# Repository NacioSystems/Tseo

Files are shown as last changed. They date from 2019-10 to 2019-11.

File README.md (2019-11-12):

# Tseo
## de NacioSystems:

Versión 2.0
Fecha: 21/10/2019

Este proyecto es un robot llamado Tseo, que resuelve laberintos. Realizado por NacioSystems (O Milladoiro):

- - - 

### Introducción:

El robot está basado en la plataforma **Pololu Zumo Arduino**, al que se le incorporan tres sensores de distancia _VL6180_, uno en el frontal, y otros dos a cada lado. Se incorpora también un encoder acoplado a la cadena de desplazamiento. Los sensores _VL6180_ están centrados en la caja soporte de baterías. Por último, aunque no necesario, se incorpora el sensor _QTR_ frontal de Pololu Zumo, que se utiliza para leer la banda de entrada en meta.

El programa lee las paredes del laberinto a través de los sensores VL, con lo que puede determinar en que dirección se puede mover (no hay pared), hacia adelante, derecha, izquierda o dar la vuelta si es necesario. Cuando avanza cuenta los pasos del encoder con lo que puede saber cuanto se mueve y determinar si ha avanzado una casilla. Por otra parte, para hacer los giros utiliza el giróscopo _L3G_ incluido en el Zumo, garantizando que los giros son completos y se encuentra en la orientación de destino. Como se indicó anteriormente, a través del sensor _QTR_ frontal el robot puede saber cuando entra en la meta.

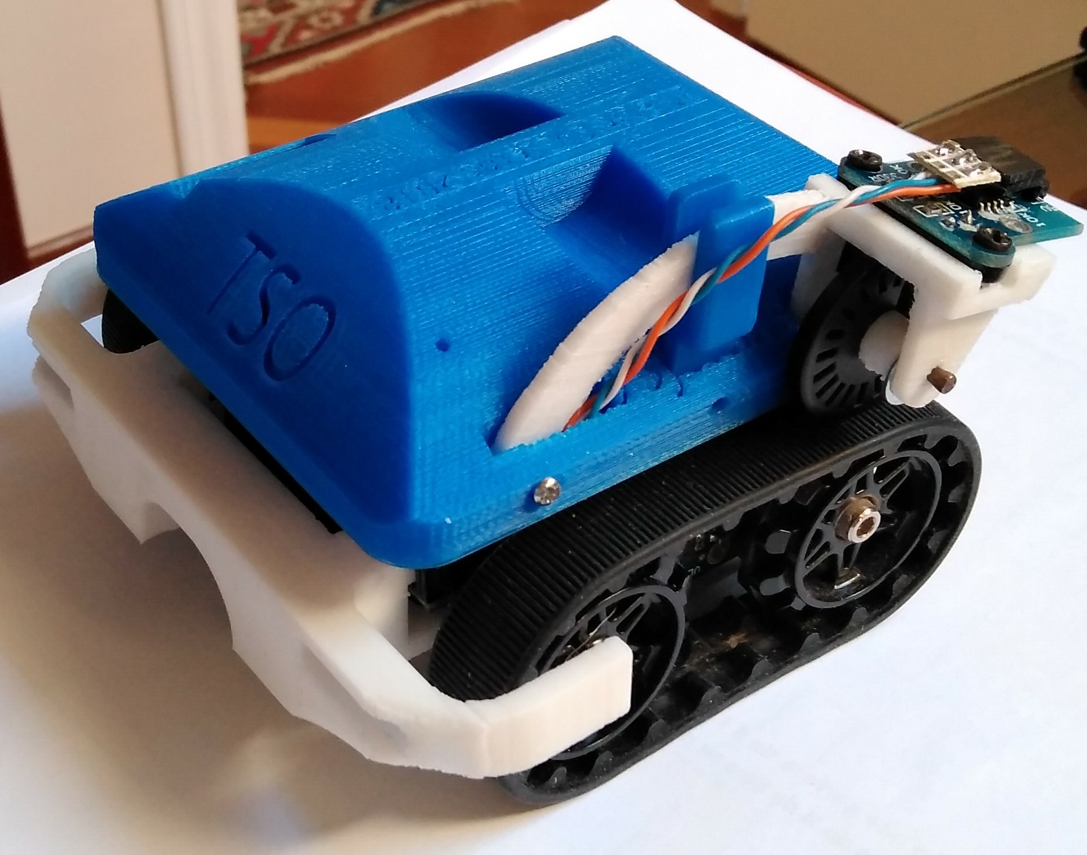
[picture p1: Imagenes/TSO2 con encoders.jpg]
Tseo Tseo listo


### Materiales:
* Pololu Zumo for Arduino (sin balda)
* Arduino UNO
* 3 x VL6180
* Zumo Reflectance Sensor Array (QTR)
* Encoder HC-020K, con rueda ranurada
* Piezas impresas 3D PLA
* Tornillos de 2mm de diámetro para sujeción Arduino y eje rueda ranurada
* Cables para conexionado, (recomendado CI perforado universal para soldar cables)

### Tablero:

El laberinto está formado por un tablero cuadrado de 256 celdas cuadradas (16x16), cada una de ellas de 18cm de lado.
El tablero está organizado en dos ejes (X, Y), de tal manera que el eje X está orientado en el sentido 0º / 180º, y el eje Y está orientado en el sentido perpendicular 90º / 270º. Para entender esta orientación pensemos en la pantalla del ordenador, 0º sería hacia arriba, 180º hacia abajo, 90º hacia la derecha y 270º hacia la izquierda. Cada vez que el robot avanza, se desplaza en el eje X o en el eje Y, de tal manera que si avanza hacia 180º, el eje X se incrementa, mientras que si avanza hacia 0º el eje X de decremeta. Por otra parte si avanza hacia la dirección 90º el eje Y se incrementa, y si avanza hacia 270º el eje Y se decrementa.

**Ejemplo de tablero y colocación de casillas (16,16), y orientación física:**

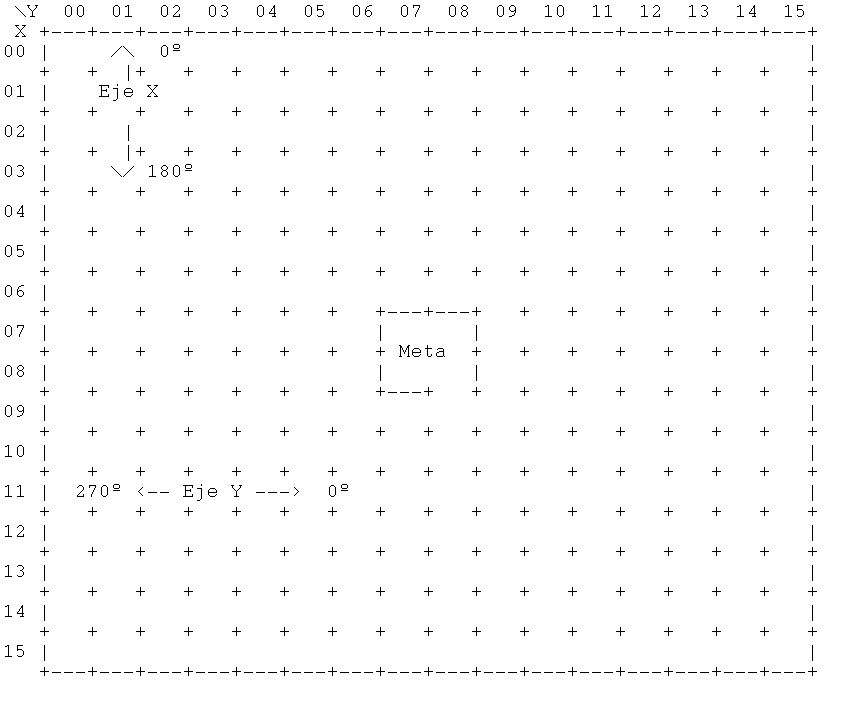
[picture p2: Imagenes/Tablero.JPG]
Tablero Tablero laberinto


### Giros:

Cada vez que el robot gira a la derecha su orientación inicial se incrementa en 90º, mientras que si gira a la izquierda su orientación inicial se decrementa 90º. No hay que decir que cuando da media vuelta supone un giro de 180º, o lo que es lo mismo dos giros de 90º. 

### Condiciones iniciales:

Se supone que la posición de inicio siempre es la misma, la casilla (0,0).
También se supone que la meta está siempre en el mismo sito, filas 7 y 8, columnas 7 y 8. La meta está cerrada totalmente a excepción de la entrada, que será siempre por la falta de muro entre las casillas (8,8) y (9,8).
El robot tendrá que saber en que orientación arranca, en sentido creciente del eje X o sentido creciente del eje Y, direcciones 180º o 90º respectivamente. Tseo utiliza el encoder, antes de inicio de la prueba, para indicarle la orientación de inicio, 180º por defecto, o 90º si se cambia.

Por otra parte Tseo, que no conoce el laberinto que va a resolver, puede elegir el sistema para recorrerlo y resolverlo entre tres opciones; regla de la mano derecha, regla de la mano izquierda o por inundación (en fase de pruebas). Para ello se utiliza el botón del Zumo, dependiendo del tiempo de pulsación de dicho botón. Una pulsación corta inicia el movimiento en base a la regla de la mano derecha, una pulsación de más de 1 segundo hace que arranque con la regla de la mano izquierda, pero si se pulsa más de 3 segundos utiliza la técnica de la inundación.

### Desplazamientos y giros:

Para los desplazamientos y giros se utilizan las rutinas de Pololu ZumoMotors y L3G TurnSensor. El robot se desplaza a la máxima velocidad que le permiten sus motores (de Minisumo), con la excepción de que tenga que hacer un giro, entonces reduce la velocidad en un 30% para compensar la inercia, que es bastante. Debido a su masa, en el momento que detecta el cambio de condiciones, por ejemplo un cruce de caminos, el robot recorre una distancia considerable después del frenazo, lo que dificulta situarse en la posición correcta para los giros. Para ello utiliza una velocidad menor y cuenta los pasos desde que toma la decisión de frenar para saber si está bien situado. Lo mismo ocurre en los giros, controlados por giróscopo, una vez completado el giro la inercia del robot hace que gire un poco de más, sobre 2º, por lo que, en función de la velocidad de giro, hay que completar ángulos más cortos, de unos 88º.

### Programa:

El programa está realizado con el IDE Arduino, para su programación directa a través de cable USB. En la carpeta software se puede ver el programa comentado. El pineado está explicado en los comentarios, sólo es necesario montar el cableado para el encoder y los sensores VL, utilizando los pines de expansión que hay en la placa Zumo. En mi caso utilicé pines hembra en la parte exterior de la *shield* y en el puerto de expansión frontal.

Una vez configurados todos los sensores y sistemas de Tseo, el programa admite el cambio de configuración por defecto, ya sea la selección de la regla mano derecha, mano izquierda, o la conmutación de los ejes del laberinto. La selección de la regla de inicio es a través de una pulsación larga del botón de inicio. Por defecto sale en el eje *X*, pero si el laberinto es diferente se selecciona la salida en el eje *Y* mediante un giro de la rueda del encoder antes del inicio. Tseo responderá con unos pitidos de que ya está configurado.

Pulsando el botón de inicio, una pulsación corta, empieza a resolver el laberinto, de tal forma que cada vez que encuentra un cruce decide tomar una decisión que guarda en la memoria. Lo mismo en el caso de que llegue a una pared y no pueda seguir, para dar media vuelta. Cada vez que se da media vuelta sabe que ese camino que recorrió desde la última decisión es incorrecto, por lo que elimina de la memoria ese camino cambiando la penúltima decisión tomada, por otra más adecuada. De esa manera va recorriendo el laberinto y guardando las decisiones tomadas, cuando detecta que en su camino el sensor de líneas delantero reconoce el color blanco, sabe que llegó a la meta. Tambien sabe que está en la meta por la casilla en la que se encuentra, pues através del _encoder_ y los giros sabe en que posición está. Una vez en la meta se para y espera que lo coloquen en la casila de salida de nuevo para iniciar de nuevo el recorrido, esta vez por el camino más corto, teniendo en cuenta las decisiones que fue almacenando en la memoria.

Tseo podría volver sólo a la casilla de origen recorriendo el camino inverso que tiene guardado en la memoria, pero dependiendo de la complegidad del laberinto, y el tiempo de competición que resta, parece más rápido y adecuado llevarlo directamente en brazos al origen. Esta función se implementará en la siguiente versión, de tal manera que si no se recoge de la meta en un tiempo determinado, Tseo decida volver el solo.

Tseo no necesita guardar todos los giros y avances que hace en la memoria, lo que le permite ahorrar mucha RAM y dedicarla a otros asuntos. Esto es, en el caso de que esté recorriendo un pasillo sin ningún cruce, aunque tenga que hacer giros a derecha o izquierda, independientemente de las casillas que avance, seguirá el único camino posible pero no tomará nota de los giros, ya que no aportan información para resolver el labertinto.

Cuando la decisión a tomar es un giro, comprueba su orientación respecto de la marcación en grados del giróscopo y hace girar los motores uno en un sentido y el otro en el inverso, dependiendo si es un giro a derechas o a izquierdas. Va leyendo la marcación del giróscopo y hasta que no alcanza los 90º de giro, mantiene los motores en marcha.

Cuando avanza va comprobando a través de los sensores VL si tiene o no pared a la derecha, izquierda o delante, de esa manera sabe si llegó a un cruce o todavía está pasando el cruce al que había llegado.

Al final, después de recorrer todo el laberinto, hace un pequeño baile mientras toca una alegre canción.

Por otra parte, a través del encoder, que está conectado a las interrupciones (pin 2), va contando los pasos que avanza, de tal manera que recorrida la longitud de una casilla y sabiendo la orientación en la que está, actualiza su posición. De esa manera sabe en que casilla está en cada momento, y reconoce por su situación cuando está en la casilla de meta. Esta funcionalidad está pensada para utilizar el sistema de resolución por _inundación_, todavía en evaluación por las capacidades y potencia del **ATmega328P** del Arduino. Otros robots que trabajan por la regla de la _inundación_ disponen de procesadores más rápidos y potentes, hacerlo con un **ATmega328P** a 16 MHz es todo un reto.

### Construcción:

La construcción es muy sencilla, la base es la plataforma **_Pololu Zumo for Arduino_**, al que se le ha retirado la balda de Minisumo. La plataforma se complementa con un **_Arduino Uno_**, el sensor **QTR** del **_Zumo Refectance Sensor Array_**, los tres sensores de distancias **_VL6180_** y el encoder **_HC-020K_**.

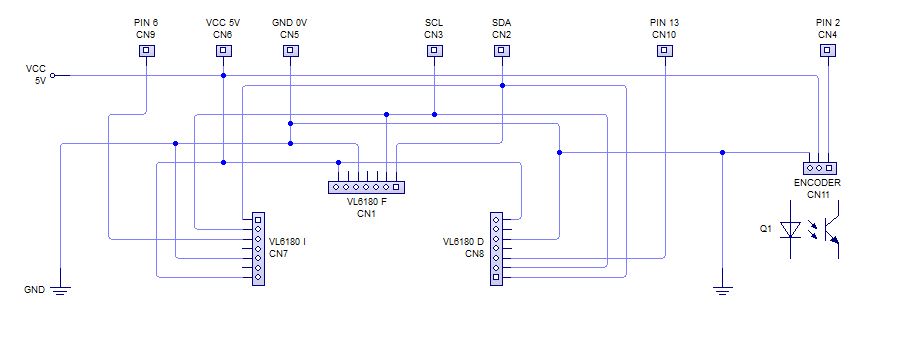
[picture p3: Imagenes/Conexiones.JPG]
Esquema de conexión


Lo único que hay que construir es el cableado de conexión de los **VL6180** y el encoder al Arduino, así como los soportes del encoder y los VL. *_La Pololu Zumo Shield for Arduino_* se encarga de realizar las conexiones con el resto de componentes, teniendo en cuenta que deberemos dejar los puentes de lectura de la tensión de la batería (A1) y del interfaz **_I2C_** (SCL, SDA), necesarios para comunicarse con el giróscopo **L3G** y los sensores **VL6180** a través de la librería _Whire_.  Para la conexión de la tarjeta _Bluetooth 5V_ es necesario montar tambien una tira de 4 pines hembra en el panel de expansión frontal izquierdo de la _shield_.  El el programa para Arduino están indicadas las conexiones de cada pin.

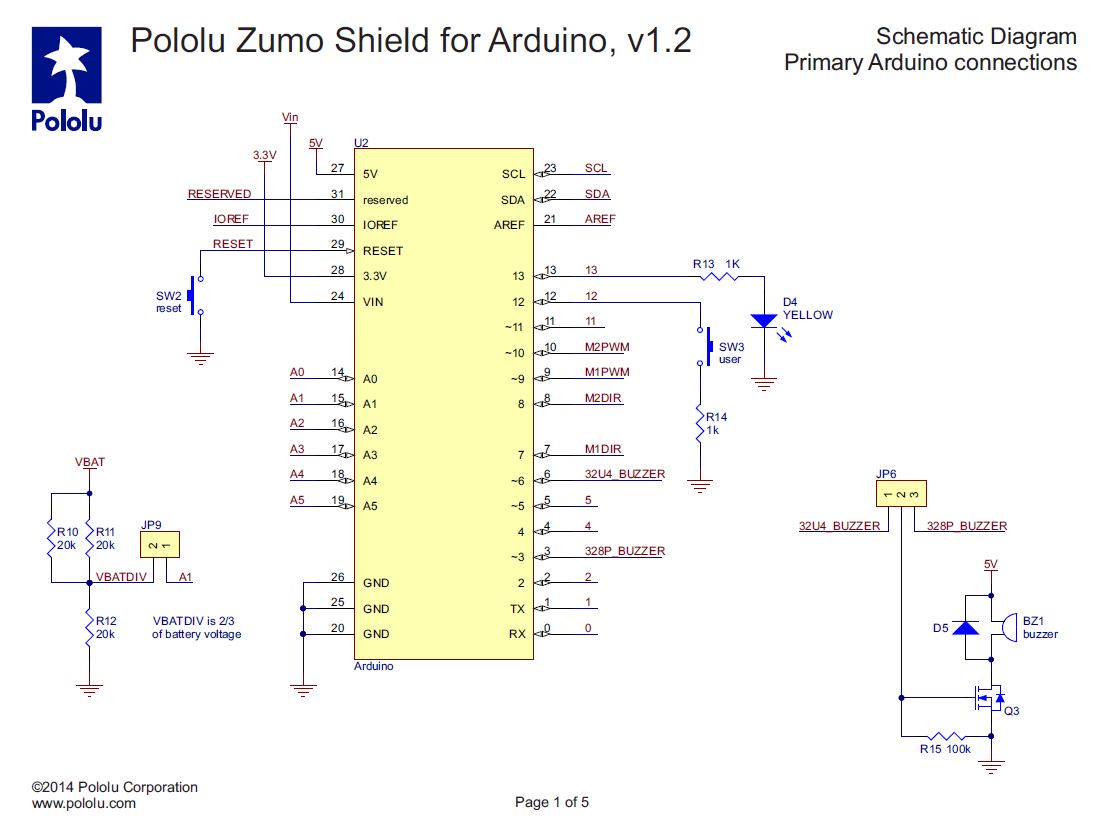
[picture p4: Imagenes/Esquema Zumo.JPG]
Esquema Zumo Arduino Esquema Pololu Zumo Arduino


Dependiendo de los motores que incorpore el Zumo, habrá que realizar ajustes a las velocidades para adaptarlas a la inercia del robot. En la fase de desarrollo me resultó imprescindible incorporarle un parachoques a Tseo, ya que las dimensiones de las cadenas hacen que en caso de derrapar o desplazamiento, las cadenas rocen con las paredes levantando al robot, creando un caos, incluso subiendo las paredes.

Tseo en construcción

La carcasa incluye un hueco muy práctico para instalar el interface _Bluetooth_ (HL05 - HL06), por si se quiere hacer un seguimiento del funcionamiento desde un terminar remoto.

También incluye un orificio para instalar un mástil, para llevar la bandera de Tseo, con la que se paseará de modo triunfante por el laberinto. El mástil puede ser un palillo de madera de los utilizados para las brochetas. La bandera está impresa en papel.

### Piezas impresas:

En la carpeta de piezas impresas, están los modelos Stl del soporte del encoder, del parachoques protector y la carcasa de Tseo, que le dan esa personalidad tan destacada.

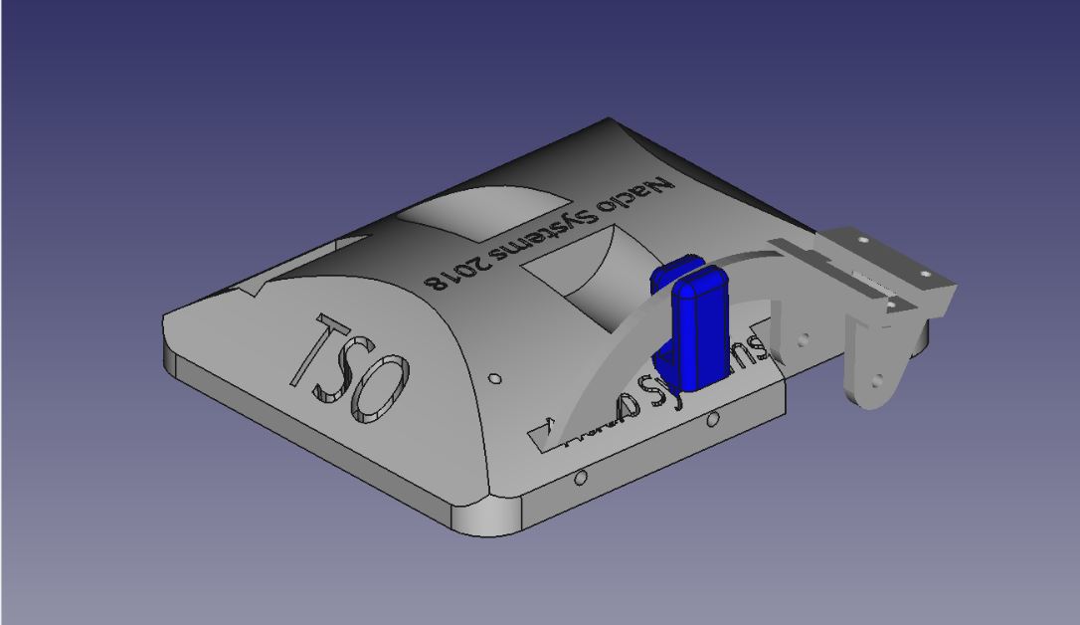
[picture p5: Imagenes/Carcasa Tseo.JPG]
Carcasa Tseo


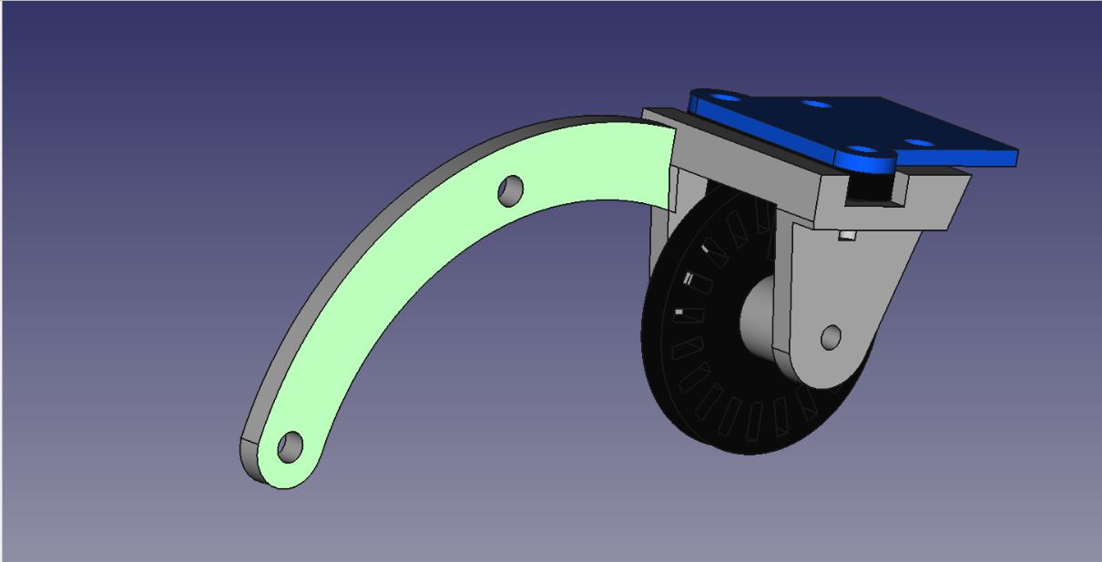
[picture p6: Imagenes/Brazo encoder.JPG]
Brazo encoder Brazo Encoder


### Referencias:

* *[Pololu Zumo for Arduino][1]*

* *[Aduino UNO R3][2]*

* *[Pololu Zumo Refectance Sensor Array][3]*

* *[Sensor LIDAR VL6180][4]*

* *[Encoder CNZ1120][5]*

* *[Encoder HC-020k][6]*

* *[Ejemplos Pololu][7]*

* *[Reglamento Laberinto OSHWDEM][8]*

### Autor:
**Ignacio Otero**

### Agradecimientos:

Muchas gracias **Bea** por tu colaboración en la revisión y corrección de esta página.

### Licencia:
Todos estos productos están liberados mediante Creative Commons Attribution-ShareAlike 4.0 International License.

[1]:https://www.pololu.com/product/2506

[2]:https://store.arduino.cc/arduino-uno-rev3

[3]:https://www.pololu.com/product/1419

[4]:https://www.adafruit.com/product/3316

[5]:https://tienda.bricogeek.com/componentes/39-fotointerruptor-cnz1120.html

[6]:https://www.amazon.es/Velocidad-HC-020K-Medici%C3%B3n-fotoel%C3%A9ctrico-Encoders/dp/B00MA63ZCW

[7]:https://github.com/pololu/zumo-shield

[8]:http://rules.oshwdem.org/labirinto_es

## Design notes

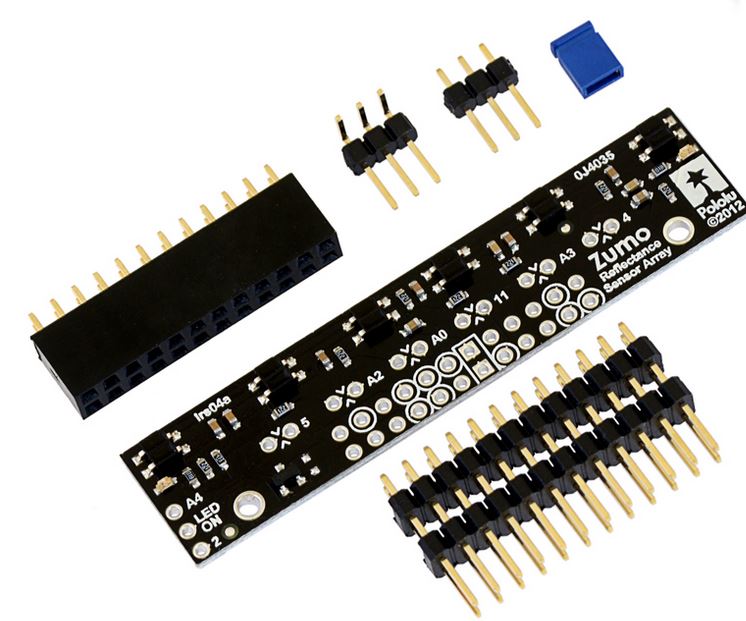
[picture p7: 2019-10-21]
Imagenes/QTR.JPG

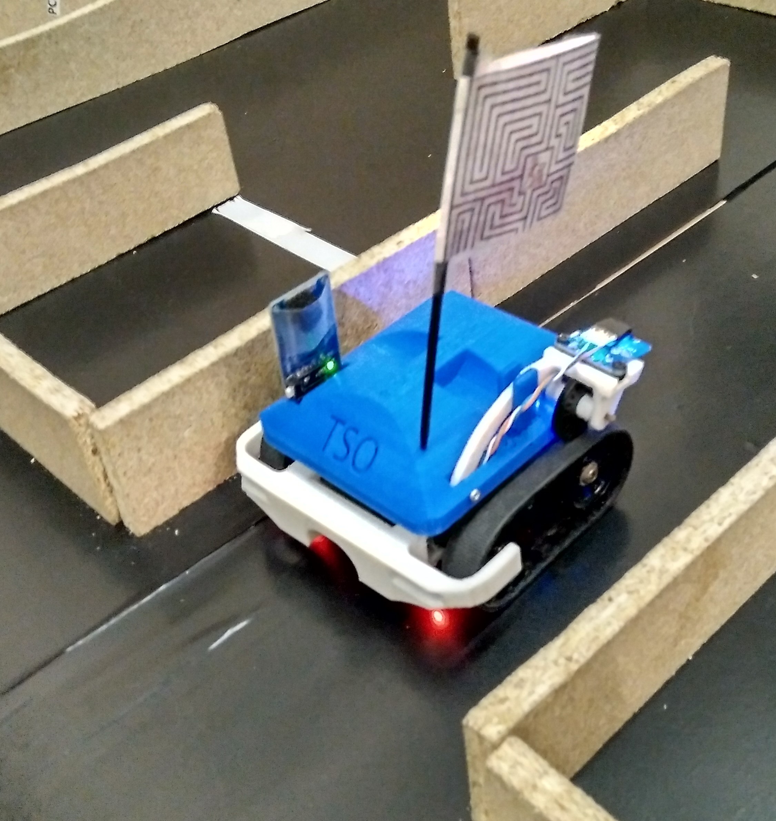
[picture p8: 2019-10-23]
Imagenes/Tseo en laberinto.jpg

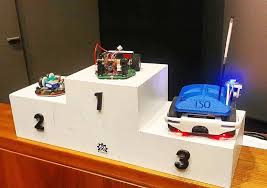
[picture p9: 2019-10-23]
Imagenes/Premios 2018.jpg

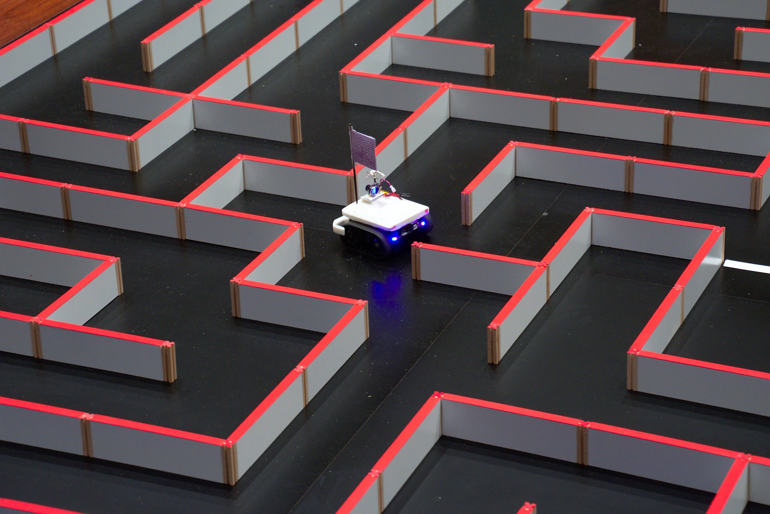
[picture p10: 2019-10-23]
Imagenes/Teseo 1 en Oshwden 2018.JPG

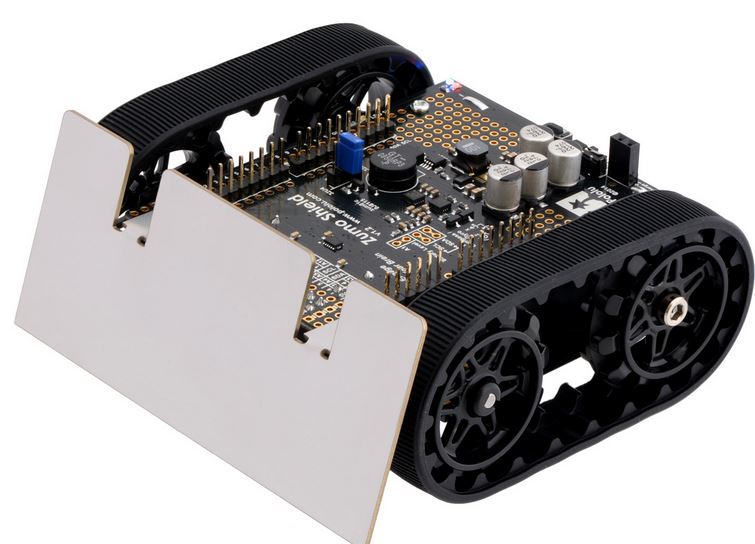
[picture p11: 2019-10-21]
Imagenes/Zumo2.JPG

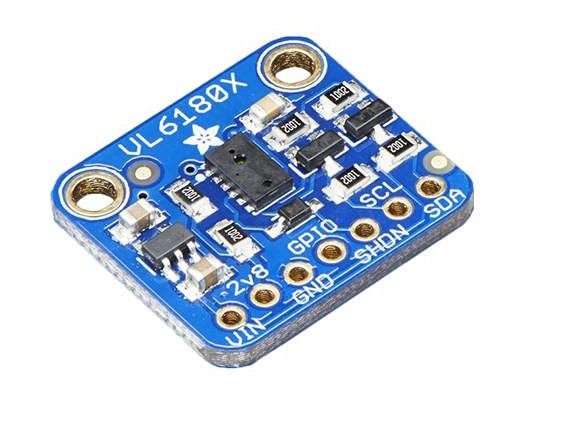
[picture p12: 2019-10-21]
Imagenes/VL6180.JPG

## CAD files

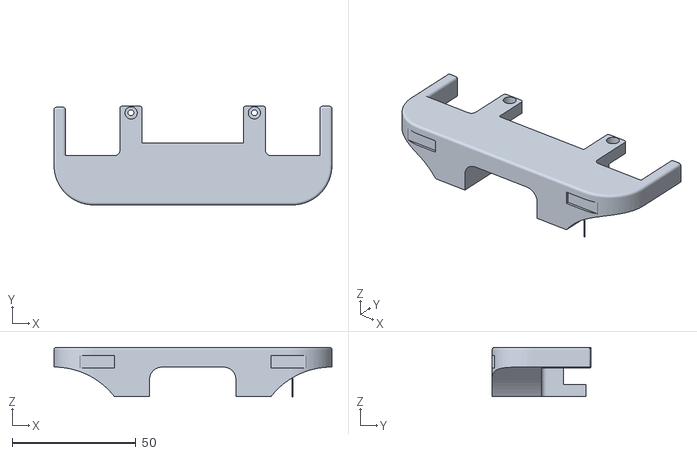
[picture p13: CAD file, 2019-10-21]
Partes Impresas/Parachoques.stl
112.6 x 40.0 x 20.0

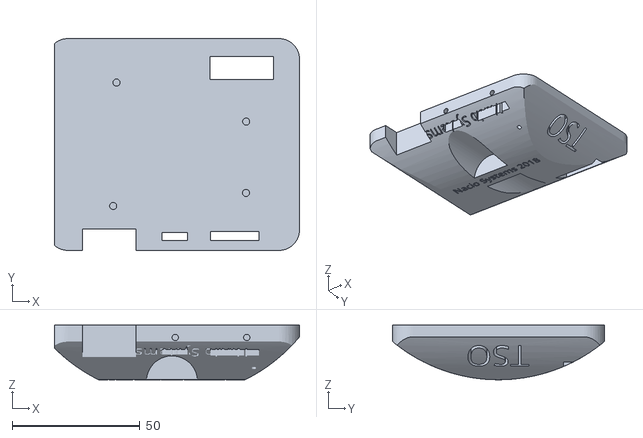
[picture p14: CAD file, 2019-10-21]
Partes Impresas/Cuerpo.stl
95.9 x 82.9 x 21.4

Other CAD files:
Partes Impresas/Brazo Encoder.stl

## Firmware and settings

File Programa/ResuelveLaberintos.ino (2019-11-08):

// RESUELVE LABERINTOS
// VERSIÓN 8.0 29/10/2018
// Por Ignacio Otero
// Ayuda de la idea de Pololu

// PINES USADOS EN ESTA VERSIÓN (19)
// BlueTooth y Serial (2) = 0, 1
// Motores Zumo (4) = 7, 8, 9, 10
// Sensor IR Zumo (7) = A0, A2, A3, 2, 4, 5, 11
// Buzzer Zumo (1) = 3 
// LED sólo en el setup, es compartido con Shutdown VLD (1) = 13 
// Pulsador Pushbutton Zumo (1)= 12
// Shutdown de sensores LIDAR VL medidores de distancia (1) = 6, 13
// Batería Zumo (1) = A1 afectado por jumper de batería
// I2C (2) = A4, A5
// Lector de interrupciones 0 por pin 2 para contar los pasos
// Si es necesario se puede utilizar A1 desconectando el jumper de la batería
// En caso de necesidad podría utilizarse los pines 7 y 8 (MDir1/2)
// como salidas digitales, siempre con motores parados o QTRSensor desactivado.

// CONFIGURACIÓN

// Para manejar el giróscopo L3G necesitamos I2G, librerias Wire
#include <Wire.h>
#include <L3G.h> // Consume 13 bytes
#include <TurnSensor.h> /* Esta librería requiere que se denomine
                        la clase L3G como "gyro", ya que es el nombre
                        que utiliza. Consume 69 bytes.
                        Se elimina de la librería TurnSensor el encendido del Led
                        Nombres de variables o constantes utilizados que no aparecen 
                        en el programa pero vienen definidos en las librerías:

                        ZUMMO_BUTTON es el nombre del botón del Zumo, pin 12

                        turnAngle    es una varible de la librería TurnSensor que
                                     indica el ángulo de giro relativo
                                     desde la medición anterior
          
                        turnAngle1   es una constante que representa el valor
                                     del giro de aproximadamente un ángulo de 1 grado
                                     Pololu recomienda que para un ángulo de 45º, se
                                     representa por el valor 0x20000000. 
                                     Un grado serían 45 veces menos.
           
                        turnRate     es la velocidad de giro instantánea, respecto de la
                                     velocidad anterior, en unidades de 0,07 grados por s.
                                     Se representa entre -180º y 180º, en sentido contrario
                                     a las agujas del reloj
                                     */

#include <VL6180X.h>    // Es la libreria de Polulu para los sensores LIDAR VL

// Tambien incluimos las librerias de Zumo
#include <ZumoMotors.h> // Consume 2 byte de memoira OK
#include <ZumoBuzzer.h> // Consume 2 bytes de memoria OK
#include <Pushbutton.h> // Consume 8 bytes de memoria OK
#include <QTRSensors.h> // Va con ZumoReflectanteSensorArray
#include <ZumoReflectanceSensorArray.h> // Consume 60 bytes de memoria


#define Parada 0
#define turnSpeed 200     
#define straightSpeed 200 
#define adjustSpeed 150
#define LED 13
#define QTREmiterPin 2  

#define RANGE 1
#define VLIzquierda 0x29     //0010 1001 Address I2C Izquierda
#define VLDerecha 0x30       //0011 0000 Address I2C Derecha
#define VLFrontal 0x46       //0100 0110 Address I2C Frontal 
#define TIzquierda 6         // Shutdown del sensor Izquierda
#define TDerecha 13          // Shutdown del sensor Derecha

// Definimos el giróscopo
L3G gyro; // Esta denominación para el L3G es necesaria por
          // la librería TurnSensor.h.

// Definimos motores
ZumoMotors motors;

// Definimos un altavoz buzzer
ZumoBuzzer buzzer;

// Definimo el pulsador de arranque
Pushbutton button(ZUMO_BUTTON); //Turnsensor utiliza el nombre de button

#include <avr/pgmspace.h>  // Esto nos permite referirnos a datos en el espacion de programa (i.e la flash)
// almacenando esta fuga en el espacio de programa usando la macro PROGMEM.  
// Despues podremos tocar directamente desde el espacio de programa, sin necesidad de cargarlo
// todo en la RAM primero.
const char fugue[] PROGMEM = 
  "! O5 L16 agafaea dac+adaea fa<aa<bac#a dac#adaea f"
  "O6 dcd<b-d<ad<g d<f+d<gd<ad<b- d<dd<ed<f+d<g d<f+d<gd<ad"
  "L8 MS <b-d<b-d MLe-<ge-<g MSc<ac<a ML d<fd<f O5 MS b-gb-g"
  "ML >c#e>c#e MS afaf ML gc#gc# MS fdfd ML e<b-e<b-"
  "O6 L16ragafaea dac#adaea fa<aa<bac#a dac#adaea faeadaca"
  "<b-acadg<b-g egdgcg<b-g <ag<b-gcf<af dfcf<b-f<af"
  "<gf<af<b-e<ge c#e<b-e<ae<ge <fe<ge<ad<fd"
  "O5 e>ee>ef>df>d b->c#b->c#a>df>d e>ee>ef>df>d"
  "e>d>c#>db>d>c#b >c#agaegfe f O6 dc#dfdc#<b c#4";

// Definimos el sensor delantero QTR
// Definimos una clase de sernsor reflectante frontal, sin pin de emisión, no apaga los IR Leds
ZumoReflectanceSensorArray sensorIR(QTREmiterPin); 

// Definimos un array para almacenar los valores del sensor
#define NUM_SENSORES 6
unsigned int ValoresSensor[NUM_SENSORES];
#define NIVEL_DISPARO_QTR  300 // Es el valor de decisión, en microsegundos, tenía anteriormente 300 para borde blanco, 900 cartón marrón borde negro
                               // Hay que pensar que el Dohyo es negro y la línea blanca

// Definimos sensores VL y configuración
VL6180X sensorI; // Izquierda
VL6180X sensorD; // Derecha
VL6180X sensorF; // Frontal


char Camino[250]; //={'L','F','F','L'}; // Camino="LFFL"
uint8_t Long_Camino = 0; //4 // Es la longitud del camino, máximo 250

bool regla=true; // Por defecto es la regla de la mano izquierda
                 // si fuera falso seria la mano derecha

unsigned long tiempo=0; // En nicio para seleccionar regla mano iz o der.
unsigned long IncTiempo=0; // Es para otras posibiliades
int32_t alfa=0; // Giros de 90º. Se pueden hacer otros.
double angulo;  // Para el cálculo de ángulos por la diagonal

// POSICIONAMIENTO DEL ROBOT EN EL TABLERO
// Contador pasos al andar de frente
// Variables volátiles para utilizar en las interrupciones
// en un primer cálculo cada paso anda 0,168111 cm.
// Una celda de 18cm tendría 107 pasos de largo
volatile long contador = 0;
// Es el espacio recorrido total
// Una casilla son 18cm, un giro 0
// Cada vez que se llama a Siguesegmento suma 18
uint16_t ContadorTotal=0; 

int derechoMovimiento = 0;    // En los cambios de velocidad de los motores
int izquierdoMovimiento = 0;  // utlizamos estas variables
boolean luces = LOW;          // Indica luces encendidas o apagadas
uint8_t distancia = 0;        // Es para la distancia frontal
uint8_t N_pasillos = 0; // Contamos el número de pasillos / opiciones en intersecciones
bool pasilloIzquierda=false, pasilloRecto=false, pasilloDerecha=false; // Nos van a indicar si hay pasillos
int Velocidad =-300; // Se puede eliminar cuando eliminemos el control por BT
bool META=false; // Nos va a decir si llegamos a la meta

// Dirección de movimiento
// Por defecto el robot sale en dirección eje x desde (0,0)
int OR_Inicio=0;
int orientacion=OR_Inicio; // Es la direción en la que se mueve el robot partiendo de (0,0)
                           // Puede ser robot en direccion eje x Or_Inicio=0, o eje y Or_Inicio=270
                           // Guardamos Or_inicio para conocer la dirección de origen en segundas
                           // El eje x se incrementa en dirección 0 y decrementa en 270
                           // El eje y se incrementa en dirección 270 y decrementa en 90
// Coordenadas de posición (x,y)
// x e y en el rango 0-15
int8_t x=0,y=0;          

void setup()
{
    // Inicializamos el serial
    Serial.begin(9600);
 
    // Proceso de configuración
    Serial.println(F("\n\n-------------------------------------------"));
    Serial.println(F("Configuración Zumo, versión 8.0, 29/10/2018"));
    Serial.println(F("             Ignacio Otero"));
    Serial.println(F("-------------------------------------------\n\n"));
  
    // Ponemos las interrupciones en el pin 2
    attachInterrupt(0, Pasos, RISING);  // Asociamos la interrupción del pin 2 a la función pasos
    
    // Inicializamos la librería wire
    Wire.begin();
   
       
    // Paramos motores
    motors.setSpeeds(0, 0);
 
    // CONFIGURAMOS SENSORES VL
    Serial.println("Configurando sensores");
    pinMode(TIzquierda,OUTPUT);
    pinMode(TDerecha,OUTPUT);
    digitalWrite(TIzquierda, LOW); // Izquierda
    digitalWrite(TDerecha, LOW); // Derecha

      delay(50);
      sensorF.init();
      sensorF.configureDefault();
      sensorF.setAddress(VLFrontal);
      Serial.print("F ADD =0x");
      Serial.println(sensorF.readReg(0x212),HEX);
      sensorF.writeReg(VL6180X::SYSRANGE__MAX_CONVERGENCE_TIME, 30);
      sensorF.writeReg16Bit(VL6180X::SYSALS__INTEGRATION_PERIOD, 50);
      sensorF.setTimeout(500);
      sensorF.stopContinuous();
      sensorF.setScaling(RANGE);
      delay(300);
      sensorF.startInterleavedContinuous(100);
      delay(100);

      digitalWrite(TDerecha, HIGH);
      delay(200);
      sensorD.init();
      sensorD.configureDefault();
      sensorD.setAddress(VLDerecha);
      Serial.print("D ADD =0x");
      Serial.println(sensorD.readReg(0x212),HEX); // read I2C address
      sensorD.writeReg(VL6180X::SYSRANGE__MAX_CONVERGENCE_TIME, 30);
      sensorD.writeReg16Bit(VL6180X::SYSALS__INTEGRATION_PERIOD, 50);
      sensorD.setTimeout(500);
      sensorD.stopContinuous();
      sensorD.setScaling(RANGE); // configure range or precision 1, 2 oder 3 mm
      delay(300);
      sensorD.startInterleavedContinuous(100);
      delay(100);

      digitalWrite(TIzquierda, HIGH);
      delay(200);
      sensorI.init();
      sensorI.configureDefault();
      //sensorI.setAddress(VLIzquierda); // El último por defecto es el 0x29
      Serial.print("I ADD =0x");
      Serial.println(sensorI.readReg(0x212),HEX);
      sensorI.writeReg(VL6180X::SYSRANGE__MAX_CONVERGENCE_TIME, 30);
      sensorI.writeReg16Bit(VL6180X::SYSALS__INTEGRATION_PERIOD, 50);
      sensorI.setTimeout(500);
      sensorI.stopContinuous();
      sensorI.setScaling(RANGE);
      delay(300);
      sensorI.startInterleavedContinuous(100);
      delay(100); 
 
     Serial.println(F("Sensores LIDAR Listos! \n"));
     delay(100);


    
 //Calibramos el giróscopo
 Serial.println("Calibrando Giroscopo");
 turnSensorSetup();  // Inicializamos el giróscopo y lo calibramos
                    
                     
  // Avisamos que está todo configurado y hay que pulsar botón
  buzzer.playNote(NOTE_G(5), 200, 15);
  Serial.println(F("L3G calibrado y listo. \n"));
 
  turnSensorReset(); // Resetamos los valores iniciales
                                          
   
    pinMode(LED,OUTPUT);
    digitalWrite(QTREmiterPin, LOW);
    
    
    char S ='P';
    for(int cont = 0; cont<100; cont++) 
      {
        if (Serial.available()) S=Serial.read();
        delay(50);
      }

    // Comprobamos estado de la batería
    Serial.print(F("Voltaje por pila = "));
    Serial.print(readBatteryMillivolts()/4);
    Serial.println(F("mV \n"));

    Serial.println(F("Pulsa boton Zumo"));
    buzzer.playNote(NOTE_A(5), 200, 15);
    delay(300);
    buzzer.playNote(NOTE_A(5), 200, 15);
    while (!button.isPressed());  // Espera a que se pulse el botón
    {
        delay(10);         
    } 
    tiempo=millis(); // Tomamos referencia del tiempo
    
    while (button.isPressed());  // Espera a que se libere el botón
    {
        delay(10);
    }

    if((millis()-tiempo)>1000) 
    {
        regla=false; // Pasamos a utilizar la mano derecha
        buzzer.playNote(NOTE_A(5), 200, 15);
        delay(300);
        buzzer.playNote(NOTE_A(5), 200, 15);
        delay(300);
        buzzer.playNote(NOTE_A(5), 200, 15);
        Serial.println(F("Pasamos a la regla de la mano derecha."));
    }
    else Serial.println(F("Por defecto regla de la mano izquierda."));
    
    Serial.println(F("Listos, resolvemos laberinto..."));

    // RESOLVEMOS EL LABERINTO
    ResuelveLaberinto();
}


void loop()
{
// El laberinto está resulto. Esperamos a que se pulse un botón.
  button.waitForButton();

  // Seguimos el camino simplificado calculado antes para alcanzar el final
  // del laberinto.
  SigueCaminoLaberinto();
}

// FUNCION Girar()
// Gira de acuerdo al parámetro Direccion, el cual podra ser 'L'
// (izquierda), 'R' (derecha), 'F' (recto) o 'B' (atrás). Giramos
// usando el giroscopo hasta que sobrepasamos el ángulo correspondiente
// -90º, +90º, 0º o 180º.
void Girar(char Direccion) //turn(char dir)
{
     
    turnSensorReset(); // Inicializamos turnRate y turnAngle
   
    if (Direccion == 'F')
      {
          return;
      }

    switch(Direccion)
       {
         case 'B':
             motors.setSpeeds(turnSpeed, -turnSpeed);
           while((int32_t)turnAngle <= turnAngle45 * 2)
             {
               turnSensorUpdate();
             }
           delay(100);
           
           turnSensorReset();
           motors.setSpeeds(turnSpeed, -turnSpeed);
           while((int32_t)turnAngle <= turnAngle45 * 2)
            {
               turnSensorUpdate();
            } 
           break;

         case 'L':
           motors.setSpeeds(turnSpeed, -turnSpeed);
           while((int32_t)turnAngle <= turnAngle45 * 2)
             {
               turnSensorUpdate();
             }
           break;

         case 'R':
           motors.setSpeeds(-turnSpeed, turnSpeed);
           while((int32_t)turnAngle >= -turnAngle45 * 2)
             {
               turnSensorUpdate();
             }
           break;

     } // Fin del Switch
     
     // Hemos hecho el giro y paramos motores 
     motors.setSpeeds(0, 0);
} // Fin de la función

// FUNCION TomarDecision()
// Esta funcion decide el camino durante la fase de aprendizaje
// en la resolucion del laberinto.  Utiliza las variables found_left,
// found_straight, and found_right, que indican cukndo hay una salida en cada
// una de las tres direcciones, aplicando la estrategia de la regla de la mano izquieda
char TomarDecision(bool pasilloIzquierda, bool pasilloRecto, bool pasilloDerecha, bool regla)
{
    
  if(regla) // Estrategia de la mano izquirda
  {
       if(pasilloIzquierda) { return 'L'; }
       else if(pasilloRecto) { return 'F'; }
       else if(pasilloDerecha) { return 'R'; }
       else { return 'B'; }
  }
  else  // Estrategia de la mano derecha
  {
      if(pasilloDerecha) { return 'R'; }
      else if(pasilloRecto) { return 'F'; }
      else if(pasilloIzquierda) { return 'L'; }
      else { return 'B'; }
  }
}

     
// FUNCION CuentaPasillos()
// Esta función se encarga de comprobar los sensores en los pasillos
// y determinar si la calle está abierta en cada dirección, izquierda
// frente y derecha. Guarda los valores en las variables boolenas correspondientes
// y devuelve un valor con el número de pasillos que encuentra.
uint8_t CuentaPasillos()
{     
    
     N_pasillos = 0; // Inicializamos variables
     pasilloIzquierda=false ;
     pasilloRecto=false ;
     pasilloDerecha=false;
     
     if(sensorI.readRangeContinuousMillimeters()>120)
          {
            pasilloIzquierda=true ;
            N_pasillos++;
          }
     if(sensorF.readRangeContinuousMillimeters()>120)
          {
            pasilloRecto=true ;
            N_pasillos++;
          }
     if(sensorD.readRangeContinuousMillimeters()>120)
          {
            pasilloDerecha=true;
            N_pasillos++;
          }
     return N_pasillos;
}   


// FUNCION ResuelveLaberinto()
// La función ResuelveLaberinto() trabaja simplificando
// la estrategia de la mano izquierda. El robot sigue un segmento
// hasta que alcanza una intersección, donde debe tomar el camino
// más a la izquieda. Guarda cada giro que hace, y si el laberinto
// no tiene bucles, esta estrategia llevará eventualmente al final.
// Despues, el camino recorrido se simplificará eliminando
// las calles muertas.
void ResuelveLaberinto()
{
   Long_Camino = 0;
 
   delay(1000);
  
   buzzer.playFromProgramSpace(PSTR("!L16 cdegreg4"));

  while(1)
  {
    SigueSegmento();
     
    AjustarInterseccion(); //Avanza itersectiondelay

  
                 if(META)
                   {
                     Serial.println("META!");
                     // LLegamos a Meta;
                     break; 
                   } 

    N_pasillos = CuentaPasillos(); 
                   
    char Direccion = TomarDecision(pasilloIzquierda, pasilloRecto, pasilloDerecha, regla);

    if ((N_pasillos > 1)||(Direccion='B'))
        {
             if (Long_Camino >= sizeof(Camino))
                {
                  while(1)
                     {
                        buzzer.playNote(NOTE_A(5), 200, 15);
                        delay(1000);
                     }
                }

             Serial.print(F("Guardamos decision: "));
             Camino[Long_Camino] = Direccion;
             Long_Camino++; // Incrementamos el puntero

             SimplificarCamino();

             MuestraCamino();

             if (Long_Camino == 2 && Camino[0] == 'B' && Camino[1] == 'B')
             {
                  buzzer.playFromProgramSpace(PSTR("!<b4"));
             }
        }
        
    
    Girar(Direccion);
    
    if (Direccion='B')
       {
        motors.setSpeeds(0,0);
        }
    delay(100); // esto lo podremos quitar
   } 

  motors.setSpeeds(0, 0);
  buzzer.playFromProgramSpace(PSTR("!>>a32"));
}

// FUNCION SigueCaminoLaberinto
// El recorrido del laberinto, siguiendo el camino guardado. Necesitamos
// detectar las intersecciones, pero no necesitamos identificar todas
// las salidas de cada una, asi que esta funcion eas más sencilla que 
// ResuelveLaberinto.
void SigueCaminoLaberinto()
{
   buzzer.playFromProgramSpace(PSTR("!>c32"));

   delay(1000);

  uint16_t i = 0;
  while(i<Long_Camino) // La última es 0 y no es una decisión
    {
  
       SigueSegmento();
       AjustarInterseccion();

       N_pasillos = CuentaPasillos(); 
                 
       char Direccion = TomarDecision(pasilloIzquierda, pasilloRecto, pasilloDerecha, regla);

       if((N_pasillos=0)||(Direccion='B')) // Se supone que nunca habrá una 'B', pero puede equivocarse
         {
          Direccion = Camino[i];
          i++; // Incrementamos i
         }
         Girar(Direccion);
     } 

   motors.setSpeeds(-straightSpeed, -straightSpeed);
  delay(700);
  
  buzzer.playFromProgramSpace(fugue);
  
  delay(1100); 
  motors.setSpeeds(0, 0);
   
 }

// FUNCIÖN SimplificarCamino()
// Simplificacion del camino Camino. La estrategia es que siempre que
// encontremos una secuencia xBx, podramos simplificarla cortando
// el final del tramo. Por ejemplo, LBL -> F, por que una simple F
// hace lo mismo que el final de camino LBL.
void SimplificarCamino()
{
   if(Long_Camino < 3 || Camino[Long_Camino - 2] != 'B')
  {
    return;
  }
  Serial.print(F("Simplificamos: "));
  MuestraCamino();

  int16_t AnguloTotal = 0;

  for(uint8_t i = 1; i <= 3; i++)
  {
    switch(Camino[Long_Camino - i])
    {
    case 'L':
      AnguloTotal += 90;
      break;
    case 'R':
      AnguloTotal -= 90;
      break;
    case 'B':
      AnguloTotal += 180;
      break;
    }
  }

  AnguloTotal = AnguloTotal % 360;
  switch(AnguloTotal)
  {
  case 0:
    Camino[Long_Camino - 3] = 'F';
    break;
  case 90:
    Camino[Long_Camino - 3] = 'L';
    break;
  case 180:
    Camino[Long_Camino - 3] = 'B';
    break;
  case 270:
    Camino[Long_Camino - 3] = 'R';
    break;
  }

  Long_Camino -= 2;
}

// FUNCION MuestraCamino()
void MuestraCamino()
{
  Camino[Long_Camino] = 0;
  Serial.print(F("Longitud = "));
  Serial.print(Long_Camino);
  Serial.print(F(" Camino = "));
  for(uint16_t i=0;i<Long_Camino;i++)
     {
       Serial.print(Camino[i]);
     }
  Serial.println(" ");
 }
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
